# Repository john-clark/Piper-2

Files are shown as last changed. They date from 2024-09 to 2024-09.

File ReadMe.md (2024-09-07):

# ReadMe

Welcome to the Piper-2 Organization Project!

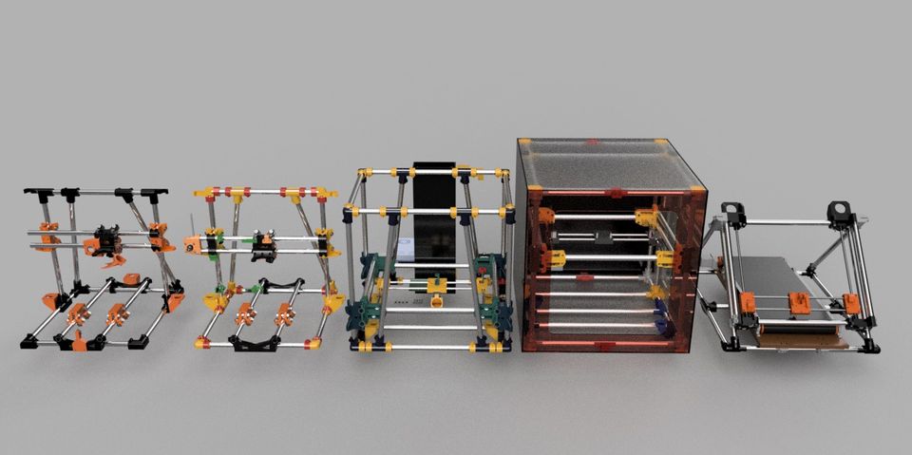
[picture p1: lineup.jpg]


## Description

Piper-3d is an exciting project that aims to revolutionize the world of low cost 3D engineering. It is a powerful tool that assists makers in high-quality 3D printer building using affordable and readily available parts. The Piper 3d printers are opensource and welcome contributions with a Creative Commons Share Alike license.

## Features

- US and European Electrical Conduit
- Different Build Platforms
- A variety of Design Features
- The latest advances in 3D printing technology

## Getting Started

To get started with Piper3D, follow these steps:

1. Clone the repository.
2. Open the Parts List table for your desired build.
3. Print and Checkoff parts as you aquire them.
4. Build your printer
5. Create new modifications and share them with others!

## Contribution

[Piper3printers](https://piper3dprinters.com/) started in 2016 by Alex Balako.

Designs are found on [Thingiverse/piper3d](https://www.thingiverse.com/piper3d/designs)

**I updated this repo to contain all the Piper3d related items I could find, so I could learn more and figure out what I need to print. This is not meant to be an official resource.*

## License

Piper-2 is licensed under the [Creative Commons - Attribution - Non-Commercial - Share Alikee](./LICENSE).

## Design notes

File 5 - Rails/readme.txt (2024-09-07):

This is work in progress on new Piper 5 3d printer

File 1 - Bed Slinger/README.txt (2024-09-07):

Piper 1 version 2 3D Printer by Piper3D on Thingiverse: 

EU - https://www.thingiverse.com/thing:2966295
US - https://www.thingiverse.com/thing:2999885

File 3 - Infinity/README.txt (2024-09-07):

Piper Infinity (Piper 4) - Infinite Z 3D Printer (Metric version or 19mm pipe)  by Piper3D on Thingiverse: https://www.thingiverse.com/thing:3817276
Piper Infinity (Piper 4) - Infinite Z 3D Printer (US version or 1/2 US EMT conduit) by Piper3D on Thingiverse: https://www.thingiverse.com/thing:3711685

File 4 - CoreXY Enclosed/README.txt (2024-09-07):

Piper 2 version 2 Enclosed CoreXY design based on EMT conduit pipes US version by Piper3D on Thingiverse: https://www.thingiverse.com/thing:3294998
Piper 2 version 2 Enclosed CoreXY design based on 20mm OD EMT conduit pipes UK by Piper3D on Thingiverse: https://www.thingiverse.com/thing:3303290

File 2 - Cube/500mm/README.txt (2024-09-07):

500mm+ upgrade for Piper 2 3d printer UK version  by Piper3D on Thingiverse: https://www.thingiverse.com/thing:3058435
500mm+ upgrade for Piper 2 3d printer US version by Piper3D on Thingiverse: https://www.thingiverse.com/thing:3051204

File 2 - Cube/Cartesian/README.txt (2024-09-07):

Piper 2 3D Printer (CoreXY design based on EMT conduit pipes) US version by Piper3D on Thingiverse: https://www.thingiverse.com/thing:3022836
Piper 2 3D Printer (CoreXY design based on EMT conduit pipes) 20mm OD Conduit version by Piper3D on Thingiverse: https://www.thingiverse.com/thing:3036472

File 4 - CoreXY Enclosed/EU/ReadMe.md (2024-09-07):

#### Summary

Piper 2.2 printing: <https://youtu.be/g6x3LBGErbc>

[Update: renamed "frame-corner-joint.stl" to "enclosure-frame-corner-joint.stl"]\
[Update: added gantry-motor-mount.nema23.stl and gantry-motor-mount.nema17.stl instead of gantry-motor-mount-.stl]\
[Update: added "gantry-Z_Rod_Nut_Holder.12mmRod.500+.stl" for 500+ build]\
[Update: combined regular and 500+ versions in one project, for parts which are different for 500+ version look for file names, which include "500+"]\
This is version 2 of Piper 2 3d printer uses 20mm OD conduit pipes. The version which uses 17.8mm OD may be found here: <https://www.thingiverse.com/thing:3294998>.\
Stepping into the area of enclosed printers with possibilities to print other materials like ABS and PolyCarbonate. Also utilizing new bearless Z bushings and new belt tension system.\
Assembly instructions are published at <https://piper3dprinters.com/?page_id=646>\
Since parts will work inside an enclosed environment with higher temperature I am using PETG as printing material.\
Printing quantities:\
6mm-belt-tensioner.stl - 2\
frame-3xcorner.stl - 8\
frame-3xcorner-bottom.stl - 8\
frame-4xcorner.stl - 4\
frame-4xcorner-bottom.stl -4\
frame-corner-joint.stl - 8\
frame-plate-holder.stl - 4\
frame-Z-motor-holder-left.stl - 2\
frame-Z-motor-holder-right.stl - 2\
frame-Z-motor-mount.stl - 4\
gantry-idlers-mount.stl - 2\
gantry-idlers-rod-holder.stl - 2\
gantry-motor-mount.stl - 2\
gantry-motor-mount-.stl - 2\
gantry-motor-rod-holder.stl - 2\
gantry-X-carriage.stl - 2\
gantry-Y-carriage.stl - 4\
gantry-ZRod-nut-holder.stl - 4\
gantry-Z-slider.stl - 4\
joint bracket.stl - 48\
bed mounting bracket 2.stl - 4\
bed mounting bracket.stl - 4\
gantry-X carriage-extruder mount fan blower.stl - 1\
gantry-X carriage-Fan holder.stl - 1\
gantry-X carriage-Heater holder.v1.2.stl - 1\
gantry-X carriage-Wire Holder.stl - 1\
gantry-Z Bracket.stl - 4\
universal pipe bracket.stl - 1 (For Z mechanical sensor mount.stl)\
Z mechanical sensor mount.stl - 1\
Y Sensor pin.stl - 1\
Join Piper builders on FB <https://www.facebook.com/groups/258663638022956/>

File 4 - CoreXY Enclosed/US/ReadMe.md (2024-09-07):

#### Summary

Piper 2.2 printing: <https://youtu.be/g6x3LBGErbc>\
[Update 02/20/2022] If you have difficulty downloading, files are also available at <https://github.com/piper3d?tab=repositories>\
[Update: Changing license and releasing source files]\
[Update: renamed "frame-corner-joint.stl" to "enclosure-frame-corner-joint.stl"]\
[Update: added gantry-X_carriage-Sensor_Pin.stl and X End Stop sensor mount mounts on Y carriage).stl]\
[Update: added gantry-motor-mount.nema23.stl and gantry-motor-mount.nema17.stl instead of gantry-motor-mount-.stl]\
[Update: added "gantry-Z_Rod_Nut_Holder.12mmRod.500+.stl" for 500+ build]\
[Update: combined regular and 500+ versions in one project, for parts which are different for 500+ version look for file names, which include "500+"]

Autodesk Fusion project for classic <https://a360.co/3qXlmPG>\
Autodesk Fusion project for enclosed <https://a360.co/3uo7hNz>\
or download igs files in "Piper 2.2 Classic v2.zip"

This is version 2 of Piper 2 3d printer. Stepping into the area of enclosed printers with possibilities to print other materials like ABS and PolyCarbonate. Also utilizing new bearless Z bushings and new belt tension system.

Assembly instructions are published at <https://piper3dprinters.com/?page_id=646>

Since parts will work inside an enclosed environment with higher temperature I am using PETG as printing material.

Printing quantities:\
6mm-belt-tensioner.stl - 2\
frame-3xcorner.stl - 8\
frame-3xcorner-bottom.stl - 8\
frame-4xcorner.stl - 4\
frame-4xcorner-bottom.stl -4\
frame-corner-joint.stl - 8\
frame-plate-holder.stl - 4\
frame-Z-motor-holder-left.stl - 2\
frame-Z-motor-holder-right.stl - 2\
frame-Z-motor-mount.stl - 4\
gantry-idlers-mount.stl - 2\
gantry-idlers-rod-holder.stl - 2\
gantry-motor-mount.stl - 2\
gantry-motor-mount-.stl - 2\
gantry-motor-rod-holder.stl - 2\
gantry-X-carriage.stl - 2\
gantry-Y-carriage.stl - 4\
gantry-ZRod-nut-holder.stl - 4\
gantry-Z-slider.stl - 4\
joint bracket.stl - 48\
bed mounting bracket 2.stl - 4\
bed mounting bracket.stl - 4\
gantry-X carriage-extruder mount fan blower.stl - 1\
gantry-X carriage-Fan holder.stl - 1\
gantry-X carriage-Heater holder.v1.2.stl - 1\
gantry-X carriage-Wire Holder.stl - 1\
gantry-Z Bracket.stl - 4\
universal pipe bracket.stl - 1 (For Z mechanical sensor mount.stl)\
Z mechanical sensor mount.stl - 1\
Y Sensor pin.stl - 1

Join Piper builders on FB <https://www.facebook.com/groups/258663638022956/>

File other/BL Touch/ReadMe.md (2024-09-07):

#### Summary

[Update: Added new version of the slider. got tired of them breaking and being inconsistent]\
This is a remix of "BlTouch Adjustable Mount" with adjusting screw of Imperial #6 size. Fits Piper 2 3D Printer.

For the adjustment mechanism you will need:\
1 - #6 2'' screw\
3 - #6 nuts.\
To mount BL touch:\
2 - #4 1/2'' screws\
2 - #4 nuts.

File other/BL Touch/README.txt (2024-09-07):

BL Touch Adjustable Mount for Piper 2 #6 screws by Piper3D on Thingiverse: https://www.thingiverse.com/thing:3170734

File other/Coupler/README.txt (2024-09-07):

Couplers for Z motors by Piper3D on Thingiverse: https://www.thingiverse.com/thing:3096142
Z couplings for Piper 3d printers and other 3d printers. 3 sizes for M8 thread, 5/16, and 3/8th.

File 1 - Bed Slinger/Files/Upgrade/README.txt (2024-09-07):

Piper 1 3D Printer version 3 upgrade by Piper3D on Thingiverse: https://www.thingiverse.com/thing:3539464

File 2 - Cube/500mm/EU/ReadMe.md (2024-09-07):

#### Summary

Large Piper 2: <https://youtu.be/ugT5Qs-Ho4Y>\
[Update: added X carriage for new version 2.2 belt tension "gantry-X_carriage-Extruder_Holder.12mmRods.v2.2.stl" and gantry-X_carriage-10mmbelt-tensioner.stl]

[Update: added Nema 23 mount for XY]

[Update: check v3 versions for gantry corner parts, changes are for motor side previous do not hold pipes; idler side was missing nut slots]

[Update: Found that some idlers for 10mm belt may be 14mm tall, please check new versions tagged "v1.1"]

[Update: Found problems with motor and idlers mounts. Fixed now as v2 files and 3mm bore and 5mm bore idleres]

By default, Piper 2 (<https://www.thingiverse.com/thing:3022836>) is designed to use 8mm guiding rods. Guiding rods will become unstable under belt tension if bed size will be stretched larger than 300mm. This upgrade allows the use of 12 mm rods and 10 mm GT2 belt. It should allow expansion of Piper 2 to a bed size beyond 300mm for example 500x500mm. Some dimensions have changed so bed size will be 123 mm less than Y rod and 113 mm less than X rod.

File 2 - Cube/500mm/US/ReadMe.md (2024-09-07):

#### Summary

[Update: added X carriage for new version 2.2 belt tension "gantry-X_carriage-Extruder_Holder.12mmRods.v2.2.stl" and gantry-X_carriage-10mmbelt-tensioner.stl]

[Update: added Nema 23 mount for XY]

Some of UK providers are still blocking the main website (they are slow to react) you may access mirror at <http://s728416714.onlinehome.us>.

[Update: check "v2" versions for gantry corner parts, changes are for motor side previous do not hold pipes; idler side was missing nut slots]

[Update: Found that some idlers for 10mm belt may be 14mm tall, please check new versions tagged "v1.1"]

This is 19.9 or 20mm pipe version upgrade (UK version).\
By default, Piper 2 (<https://www.thingiverse.com/thing:3036472>) is designed to use 8mm guiding rods. Guiding rods will become unstable under belt tension if bed size will be stretched larger than 300mm. This upgrade allows the use of 12 mm rods and 10 mm GT2 belt. It should allow expansion of Piper 2 to a bed size beyond 300mm for example 500x500mm. Some dimensions have changed so bed size will be 123 mm less than Y rod and 113 mm less than X rod.

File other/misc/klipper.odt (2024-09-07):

# This file serves as documentation for config parameters of corexy

# style printers. One may copy and edit this file to configure a new

# corexy printer. Only parameters unique to corexy printers are

# described here - see the "example.cfg" file for description of

# common config parameters.

# DO NOT COPY THIS FILE WITHOUT CAREFULLY READING AND UPDATING IT

# FIRST. Incorrectly configured parameters may cause damage.

# The main micro-controller is used as the timing source for all the

# micro-controllers on the printer. Typically, both the X and Y axes

# are connected to the main micro-controller.

[mcu]

serial: /dev/ttyACM0

#serial: /dev/serial/by-path/pci-0000:00:14.0-usb-0:2:1.0-port0

#serial: /dev/serial/by-path/pci-0000:00:14.0-usb-0:1:1.0-port0

#pin_map: arduino

#baud: 250000

# Support manually moving stepper motors for diagnostic purposes.

# Note, using this feature may place the printer in an invalid state -

# see docs/G-Codes.md for important details.

[force_move]

enable_force_move: true

# Set to true to enable FORCE_MOVE and SET_KINEMATIC_POSITION

# extended G-Code commands. The default is false.

# The "zboard" micro-controller will be used to control the Z axis.

[mcu z]

#serial: /dev/serial/by-path/pci-0000:00:14.0-usb-0:1:1.0-port0

#serial: /dev/serial/by-path/pci-0000:00:14.0-usb-0:2:1.0-port0

serial: /dev/ttyUSB0

pin_map: arduino

baud: 250000

#test INIT_TMC STEPPER=stepper_y DUMP_TMC STEPPER=stepper_y

[board_pins]

aliases:

# EXP1 header

EXP1_1=P1.30, EXP1_3=P1.18, EXP1_5=P1.20, EXP1_7=P1.22, EXP1_9=<GND>,

EXP1_2=P0.28, EXP1_4=P1.19, EXP1_6=P1.21, EXP1_8=P1.23, EXP1_10=<5V>,

# EXP2 header

EXP2_1=P0.17, EXP2_3=P3.26, EXP2_5=P3.25, EXP2_7=P1.31, EXP2_9=<GND>,

EXP2_2=P0.15, EXP2_4=P0.16, EXP2_6=P0.18, EXP2_8=<RST>, EXP2_10=<NC>

# Pins EXP2_1, EXP2_6, EXP2_2 are also MISO, MOSI, SCK of bus "ssp0"

# stepper controlling the X+Y movement.

[stepper_y]

step_pin: P0.19

dir_pin: !P0.20

enable_pin: !P2.8

#step_distance: 0.2

step_distance: 0.0125 #SHould be 0.0125 for 1/16 micro-steppting

##step_distance: 0.00625

endstop_pin: tmc2130_stepper_y:virtual_endstop

homing_retract_dist: 0

position_endstop: 0

position_min: 0

position_max: 500

homing_speed: 60

[tmc2130 stepper_y]

cs_pin: P1.15

spi_software_miso_pin: P0.5

spi_software_mosi_pin: P4.28

spi_software_sclk_pin: P0.4

diag1_pin: !P1.27

microsteps: 16

interpolate: True

run_current: .80 #Try 0.75 to 0.85 by 0.05 increments

hold_current: .5 #Set to 0.75

stealthchop_threshold: 0

driver_PWM_GRAD: 10

driver_SGT: 4

# The stepper_y section is used to describe the Y axis as well as the

# stepper controlling the X-Y movement.

[stepper_x]

step_pin: P2.2

dir_pin: P2.6

enable_pin: !P2.1

step_distance: 0.0125 #SHould be 0.0125 for 1/16 micro-steppting

#step_distance: 0.00625

endstop_pin: tmc2130_stepper_x:virtual_endstop

homing_retract_dist: 0

position_endstop: 0

position_max: 500

position_min: 0

homing_speed: 60

[tmc2130 stepper_x]

cs_pin: P1.17

spi_software_miso_pin: P0.5

spi_software_mosi_pin: P4.28

spi_software_sclk_pin: P0.4

diag1_pin: !P1.29

microsteps: 16

interpolate: True

run_current: .80 #Try 0.75 to 0.85 by 0.05 increments

hold_current: .5 #Set to 0.75

#run_current: 1.2 #Try 0.75 to 0.85 by 0.05 increments

#hold_current: .5 #Set to 0.75

#sense_resistor: 0.110

stealthchop_threshold: 0

driver_PWM_GRAD: 10

driver_SGT: 11

[stepper_z]

# Z stepper pins on MCU Z

step_pin: z:ar60

dir_pin: z:ar61

enable_pin: !z:ar56

step_distance: 0.000625

# probe:z_virtual_endstop is a virtual pin definition only available if

# a probe section is defined

endstop_pin: probe:z_virtual_endstop

# mechanical switch on mcu Z X min endstop pin

##endstop_pin: ^!z:ar19

#position_endstop: -0.376

position_min: -5

position_max: 500

homing_speed: 5

[stepper_z1]

# X stepper pins on MCU Z

step_pin: z:ar54

dir_pin: z:ar55

enable_pin: !z:ar38

step_distance: 0.000625

[stepper_z2]

# E0 stepper pins on MCU Z

step_pin: z:ar26

dir_pin: z:ar28

enable_pin: !z:ar24

step_distance: 0.000625

[stepper_z3]

# E0 stepper pins on MCU Z

step_pin: z:ar46

dir_pin: z:ar48

enable_pin: !z:ar62

step_distance: 0.000625

#[servo toolS]

#pin: z:ar42

#maximum_servo_angle: 300

### The maximum angle (in degrees) that this servo can be set to. The

### default is 180 degrees.

##minimum_pulse_width: 0.0005

### The minimum pulse width time (in seconds). This should correspond

### with an angle of 0 degrees. The default is 0.001 seconds.

#maximum_pulse_width: 0.003

#initial_angle: 120

[probe]

pin: ^!z:ar18

z_offset: 1.82

y_offset: 5

x_offset: 0

speed: 5.0

#[homing_override]

#set_position_z: 0

#axes: z

#gcode:

# G90 ; Uncomment these 2 lines to blindly lift the Z 2mm at start

# G1 Z10 F600

# G28 X0 Y0

# G1 X250 Y250 F3600

# G28 Z0

[homing_override]

set_position_z: 0

axes: z

gcode:

G90 ; Uncomment these 2 lines to blindly lift the Z 2mm at start

G1 Z8 F600

G28 X0 Y0

G1 X250 Y250 F3600

G28 Z0

G1 Z10 F600

#[temperature_sensor Host_temp]

#sensor_type: temperature_host

#sensor_path: /sys/bus/platform/drivers/coretemp/coretemp.0/hwmon/hwmon1/temp2_input

#gcode_id:S

[adc_temperature my_sensor]

#temperature1: 28

#voltage1: 0.8

temperature1: 26.5

voltage1: 0.822

temperature2: 50.3

voltage2: 0.914

temperature3: 75.5

voltage3: 1.012

temperature4:100.6

voltage4:1.106

temperature5:150.4

voltage5:1.289

temperature6:200.1

voltage6:1.464

temperature7:225.1

voltage7:1.547

temperature8:250.8

voltage8:1.623

#temperature1: 221

#resistance1:

#temperature2:

#resistance2:

[thermistor winsinn_ht-ntc100k]

temperature1: 25

resistance1: 100000

temperature2: 80

resistance2: 8300

temperature3: 220

resistance3: 127

[extruder]

step_pin: P2.13

dir_pin: !P0.11

enable_pin: !P2.12

#step_distance: 0.010476

step_distance: 0.0024145313708312

nozzle_diameter: 0.400

filament_diameter: 1.750

max_extrude_cross_section: 20.0

max_extrude_only_distance: 950.0

max_extrude_only_accel: 10000

#pressure_advance: 0.0

#pressure_advance_lookahead_time: 0.010

#pressure_advance: 0.45

#pressure_advance_lookahead_time: 0.02

heater_pin: P2.7

######sensor_type: winsinn_ht-ntc100k

######sensor_pin: P0.24

######pullup_resistor: 4700

######sensor_type: ATC Semitec 104GT-2

sensor_type: NTC 100K beta 3950

sensor_pin: P0.24

#sensor_type: PT100 INA826

#adc_voltage: 3.2

#sensor_pin: P0.2

#voltage_offset: 0.48

#PT100

#sensor_type: my_sensor

#adc_voltage: 3.275

#sensor_pin: P0.2

#sensor_type: NTC 100K beta 3950

#sensor_type: EPCOS 100K B57560G104F

#sensor_type: NTC 100K MGB18-104F39050L32

#sensor_type: Honeywell 100K 135-104LAG-J01

#control: watermark

min_temp: 0

max_temp: 500

#[extruder1]

#step_pin: z:ar36

#dir_pin: !z:ar34

#enable_pin: !z:ar30

#step_distance: 0.0024145313708312

#nozzle_diameter: 0.400

#filament_diameter: 1.750

#max_extrude_cross_section: 20.0

#max_extrude_only_distance: 950.0

#max_extrude_only_accel: 10000

#pressure_advance: 0.0

#pressure_advance_lookahead_time: 0.010

#pressure_advance: 0.45

#pressure_advance_lookahead_time: 0.02

#heater_pin: z:ar10

#sensor_pin: z:analog13

##sensor_type: ATC Semitec 104GT-2

#sensor_type: NTC 100K beta 3950

#sensor_type: EPCOS 100K B57560G104F

#sensor_type: NTC 100K MGB18-104F39050L32

#sensor_type: Honeywell 100K 135-104LAG-J01

#control: watermark

#min_temp: 0

#max_temp: 300

#pid_Kp: 22.2

#pid_Ki: 1.08

#pid_Kd: 114

[heater_fan my_nozzle_fan]

pin: z:ar9

heater: extruder

heater_temp: 50.0

fan_speed: 1.0

[heater_bed]

heater_pin: P2.5

sensor_type: NTC 100K beta 3950

sensor_pin: P0.23

#control: watermark

min_temp: 0

max_temp: 150

[verify_heater heater_bed]

# adjust for personal bed setup, this prevents stock heated bed from issuing

# false positive heating errors due to slow temperature increase

check_gain_time: 900

[verify_heater extruder]

check_gain_time: 120

heating_gain: 1

max_error: 260

#[verify_heater extruder1]

#check_gain_time: 60

[temperature_sensor ambiant]

sensor_type: ATC Semitec 104GT-2

sensor_pin: P0.25

gcode_id:A

[fan]

pin: P2.3

# Load Multible Fans

#[include klipper/config/multiple_fans.cfg]

[printer]

kinematics: corexy

# This option must be "corexy" for corexy printers.

max_velocity: 250

max_accel: 1500

#max_z_velocity: 20

#max_z_accel: 25

max_z_velocity: 10

max_z_accel: 55

# "RepRapDiscount 128x64 Full Graphic Smart Controller" type displays

[display]

lcd_type: st7920

cs_pin: P1.19

sclk_pin: P1.20

sid_pin: P1.18

encoder_pins: ^P3.26, ^P3.25

click_pin: ^!P0.28

[output_pin beeper]

pin: P1.30

#kill_pin: ^!ar41

# Pause/Resume functionality with support of position capture and restore

[pause_resume]

recover_velocity: 50

#recover_velocity: 200

# When capture/restore is enabled, the speed at which to return to

# the captured position (in mm/s). Default is 50.0 mm/s.

# paste "unknownCommandsNeedAck: true" in ~/.octoprint/config.yaml

# serial: #

# additionalPorts: #

# - /tmp/printer #

# baudrate: 250000 #

# disconnectOnErrors: false #

# logPositionOnCancel: true #

# port: /tmp/printer #

# unknownCommandsNeedAck: true #

# Filament Switch Sensor. Support for filament insert and runout detection

# using a switch sensor, such as an endstop switch.

[filament_switch_sensor filament_sensor]

pause_on_runout: True

# When set to True, a PAUSE will execute immediately after a runout

# is detected. Note that if pause_on_runout is False and the

# runout_gcode is omitted then runout detection is disabled. Default

# is True.

runout_gcode: outoffilament

# The gcode to run after a filament runout is detected. If

# pause_on_runout is set to True this gcode will run after the PAUSE

# is complete. The default is not to run any gcode commands.

#insert_gcode:

# The gcode to run after a filament insert is detected. The default

# is not to run any gcode commands, which disables insert detection.

event_delay: 3.0

# The minimum amount of time in seconds to delay between events.

# Events triggered during this time period will be silently

# ignored. The default is 3 seconds.

switch_pin: ^z:ar15 #RAMPS Servo Pin 4

# The pin on which the switch is connected. This parameter must be

# provided.

# Idle timeout. An idle timeout is automatically enabled - add an

# explicit idle_timeout config section to change the default settings.

[idle_timeout]

#gcode:

# A list of G-Code commands (one per line; subsequent lines

# indented) to execute on an idle timeout. The default is to run

# "TURN_OFF_HEATERS" and "M84".

#timeout: 600

timeout: 1200

# Idle time (in seconds) to wait before running the above G-Code

# commands. The default is 600 seconds

#_____________________MACROS______________________________________#

#_____________________MACROS______________________________________#

[gcode_macro outoffilament]

gcode:

PARK_MACRO

;UNLOAD

M117 OUT OF FILAMENT..

[gcode_macro PARK_MACRO]

default_parameter_X: -15

default_parameter_Y: 0

default_parameter_Z: 30

gcode:

M117 PARKING..

G91

G1 E-3.14 F1500

G1 Z{Z}

G90

G1 X{X} Y{Y} F3000

[gcode_macro UNLOAD]

gcode:

G91

G1 E5.0 F1200

G1 E3.0 F1600

G1 E-25 F7000

G1 E-800 F3000

G90

[gcode_macro RESUME_MACRO]

gcode:

M117 RESUMING...

RESUME

#[gcode_macro M84]

#gcode:

# M18

# SET_KINEMATIC_POSITION

# Enable the "M118" and "RESPOND" extended commands.

[respond]

default_type: echo

# Sets the default prefix of the "M118" and "RESPOND" output to one of

# the following:

# echo: "echo: " (This is the default)

# command: "// "

# error: "!! "

# default_prefix: echo:

# Directly sets the default prefix. If present, this value will override

# the "default_type".

[gcode_macro G29]

gcode:

G28

quad_gantry_level

BED_MESH_CALIBRATE

BED_MESH_PROFILE SAVE=p1

G1 X0 Y0 Z5 F3600

[quad_gantry_level]

gantry_corners:

-90,-22.5

590,495

points:

20,40

20,440

450,440

450,40

speed: 50

horizontal_move_z: 10

max_adjust: 12

#samples: 3

#sample_retract_dist: 2.0

#[quad_gantry_level]

#gantry_corners:

# 0,0

# 300,300

## -88,-20

# 490,386

# A newline separated list of X,Y coordinates describing the

# two opposing corners of the gantry. The first entry corresponds to

# Z, the second to Z2.

# This parameter must be provided.

#points:

# 10,63

# 10,326

# 290,326

# 290,63

# A newline separated list of four X,Y points that should be probed

# during a QUAD_GANTRY_LEVEL command.

# Order of the locations is important, and should correspond to Z,Z1

# Z2, and Z3 location in order.

# This parameter must be provided.

# For maximum accuracy, ensure your probe offsets are configured.

#speed: 50

###speed: 150

# The speed (in mm/s) of non-probing moves during the calibration.

# The default is 50.

#horizontal_move_z: 10

# The height (in mm) that the head should be commanded to move to

# just prior to starting a probe operation. The default is 5

#samples: 3

# Number of probe samples per point. The defaut is 1

#sample_retract_dist: 6.0

# Distance in mm to retract the probe between samples. Default is 2.

# Mesh Bed Leveling. One may define a [bed_mesh] config section

# to enable move transformations that offset the z axis based

# on a mesh generated from probed points. Note that bed_mesh

# and bed_tilt are incompatible, both cannot be defined. When

# using a probe to home the z-axis, it is recommended to define

# a [homing_override] section in printer.cfg to home toward the

# center of the print area.

# Visual Examples:

# bed_shape = rectangular, probe_count = 3,3:

# x---x---x (max_point)

# x---x---x

# (min_point) x---x---x

# bed_shape = round, probe_count = 5, radius = r:

# x (0,r) end

# /

# x---x---x

# \

# (-r,0) x---x---x---x---x (r,0)

# \

# x---x---x

# /

# x (0,-r) start

[bed_mesh]

speed: 200

# The speed (in mm/s) of non-probing moves during the

# calibration. The default is 50.

horizontal_move_z: 10

# The height (in mm) that the head should be commanded to move to

# just prior to starting a probe operation. The default is 5.

#samples: 2

# The number of times to probe each point. The probed z-values

# will be averaged. The default is to probe 1 time.

#sample_retract_dist: 10.0

# The distance (in mm) to retract between each sample if

# sampling more than once. Default is 2mm.

mesh_min: 45,25

# Defines the minimum x,y position to probe when the bed_shape

# is 'rectangular'. Note that this refers to the nozzle position,

# take care that you do not define a point that will move the

# probe off of the bed. This parameter must be provided.

mesh_max:445,440

# Defines the maximum x,y position to probe when the bed_shape

# is 'rectangular'. Follow the same precautions as listed in min_point.

# Also note that this does not necessarily define the last point

# probed, only the maximum coordinate. This parameter must be provided.

probe_count: 4,4

## OR ##

##probe_count: 5

# For 'rectangular' beds, this is a comma separate pair of integer

# values (X,Y) defining the number of points to probe along each axis.

# A single value is also valid, in which case that value will be applied

# to both axes. 'Round' beds only accept a single integer value that is

# applied to both axes. The probe count must be odd for round beds.

# Default is 3,3 for 'rectangular' beds, and 5 for 'round' beds.

fade_start: 1

# The gcode z position in which to start phasing out z-adjustment

# when fade is enabled. Default is 1.0.

#fade_end: 10.0

fade_end: 0.0

# The gcode z position in which phasing out completes. When set

# to a value below fade_start, fade is disabled. It should be

# noted that fade may add unwanted scaling along the z-axis of a

# print. If a user wishes to enable fade, a value of 10.0 is

# recommended. Default is 0.0, which disables fade.

# disabling fade as per https://github.com/KevinOConnor/klipper/issues/1234

fade_target: 0

# The z position in which fade should converge. When this value is set

# to a non-zero value it must be within the range of z-values in the mesh.

# Users that wish to converge to the z homing position should set this to 0.

# Default is the average z value of the mesh.

split_delta_z: .025

# The amount of Z difference (in mm) along a move that will

# trigger a split. Default is .025.

move_check_distance: 5.0

# The distance (in mm) along a move to check for split_delta_z.

# This is also the minimum length that a move can be split. Default

# is 5.0.

#mesh_pps: 2,2

# A comma separated pair of integers (X,Y) defining the number of

# points per segment to interpolate in the mesh along each axis. A

# "segment" can be defined as the space between each probed

# point. The user may enter a single value which will be applied

# to both axes. Default is 2,2.

algorithm: bicubic

#algorithm: lagrange

# The interpolation algorithm to use. May be either "lagrange"

# or "bicubic". This option will not affect 3x3 grids, which

# are forced to use lagrange sampling. Default is lagrange.

bicubic_tension: .2

# When using the bicubic algorithm the tension parameter above

# may be applied to change the amount of slope interpolated.

# Larger numbers will increase the amount of slope, which

# results in more curvature in the mesh. Default is .2.

#*# <---------------------- SAVE_CONFIG ---------------------->

#*# DO NOT EDIT THIS BLOCK OR BELOW. The contents are auto-generated.

#*#

#*# [extruder]

#*# control = pid

#*# pid_kp = 21.512

#*# pid_ki = 1.304

#*# pid_kd = 88.737

#*#

#*# [heater_bed]

#*# control = pid

#*# pid_kp = 67.840

#*# pid_ki = 2.432

#*# pid_kd = 473.183

#*#

#*# [bed_mesh default]

#*# version = 1

#*# points =

#*# 0.292233, 0.530983, 0.431608, 0.330983

#*# 0.245358, 0.544733, 0.115358, -0.540267

#*# -0.080892, 0.474733, -0.063392, -1.140892

#*# -0.745267, 0.477233, 0.227233, -1.215892

#*# tension = 0.2

#*# min_x = 45.0

#*# algo = bicubic

#*# y_count = 4

#*# mesh_y_pps = 2

#*# min_y = 25.0

#*# x_count = 4

#*# max_y = 439.99

#*# mesh_x_pps = 2

#*# max_x = 444.99

#*#

#*# [bed_mesh p1]

#*# version = 1

#*# points =

#*# 0.292233, 0.530983, 0.431608, 0.330983

#*# 0.245358, 0.544733, 0.115358, -0.540267

#*# -0.080892, 0.474733, -0.063392, -1.140892

#*# -0.745267, 0.477233, 0.227233, -1.215892

#*# tension = 0.2

#*# min_x = 45.0

#*# algo = bicubic

#*# y_count = 4

#*# mesh_y_pps = 2

#*# min_y = 25.0

#*# x_count = 4

#*# max_y = 439.99

#*# mesh_x_pps = 2

#*# max_x = 444.99

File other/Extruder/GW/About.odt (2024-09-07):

#### Summary

I like GW extruder and saw some ways to improve it. Indeed all my current Piper printers (https://www.thingiverse.com/thing:2794632) are running on this version or AJGW extruders.
Problems I tried to fix are: E3D hotend is mounted on 2 screws and moves after some use; closing filament clamp (compressor... name it) may jam filament. Have added a new fast release, which works better for me opens and closes easier. Included mounts for Bowden tube and for E3D hotend.
Autocad Fusion 360 project may be found at: https://a360.co/2Iu8v5x or downloaded as part of all files. Autocad assembly contains components from McMaster webpage, E3D from https://www.thingiverse.com/thing:341689 , and I do not remember the source of NEMA 17 component.

Quick release in action: https://youtu.be/Ad7Fl6Ia978

As noted by Alain idler mount, which I call "filament compressor" may need to be printed on a side.

You may also check my website https://piper3dprinter.com for other things I do.

#### Post-Printing

You will also need:
3 - 608 ball bearings
1 - 18mm pin (may be a rod cut from a bolt) 5/16 or M8 to mount ball bearing in the "compressor" (idler)
2 - M4 50mm not fully threaded bolts for quick release
2 -1/4 in x0.5 in x0.035 in (6.4 mm x12 mm x0.9mm) (maybe other which will slide on M4 and held by M4 head) compression springs
1 - Nema 17 motor
1 - Hobbed bolt 5/16 or M8 (check my things for a tool to make one)
2 - nuts 5/16 or M8 to lock hobbed bolt
3 - M3 8mm bolts to hold the motor
1 - #6 1.5 in or M4 30 mm bolt and nut to hold idler ("compressor")
2 - #4 3/4 in or M3 18-20mm screws and nuts for E3D or Bowden mount.

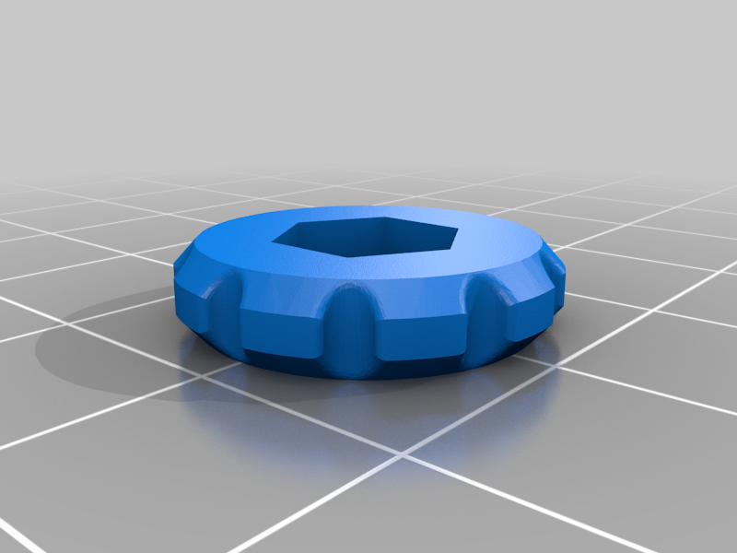
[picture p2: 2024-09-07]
other/BL Touch/images/ed52c49a278d1c5375fa5901e04589cf.png

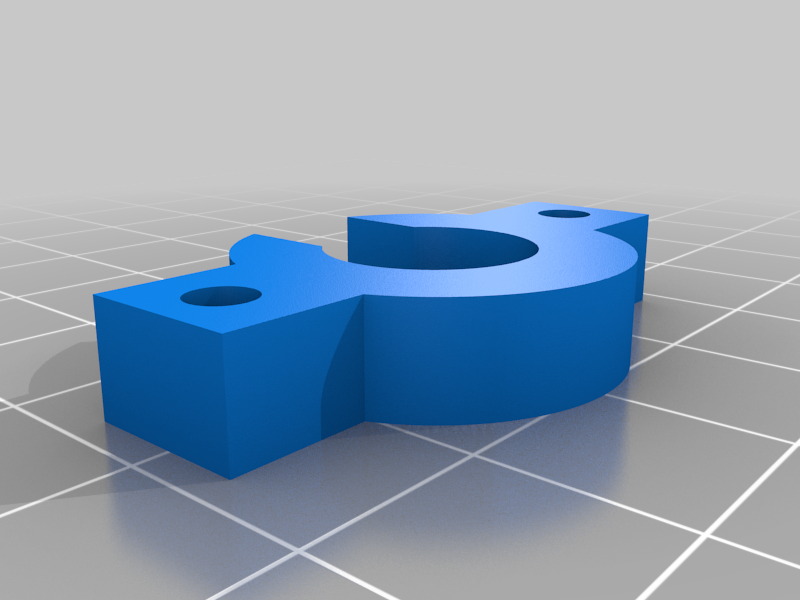
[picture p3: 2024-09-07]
other/Extruder/GW/images/3adc9352149461a922bf1bfca814c3d4.png

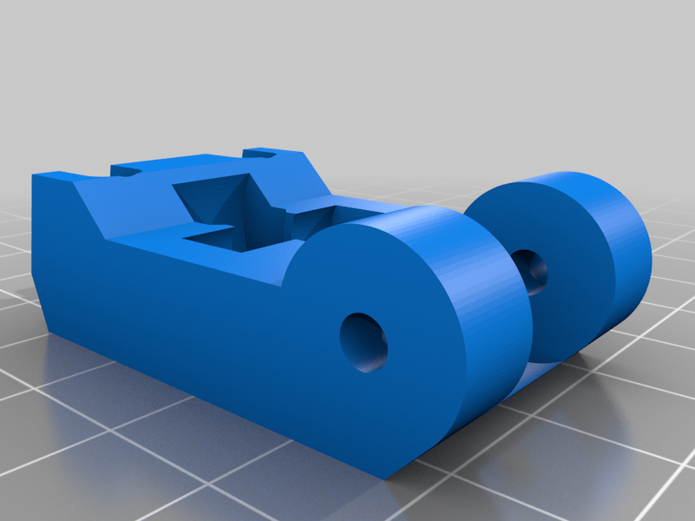
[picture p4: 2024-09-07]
other/Extruder/GW/images/1d85b2dbc3a063c84c43cf215b9fdd03.png

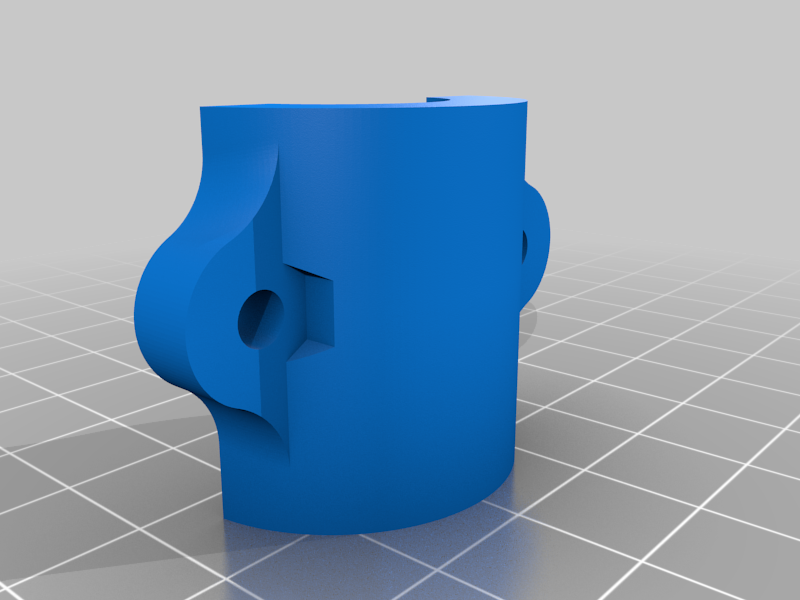
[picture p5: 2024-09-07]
other/Extruder/Titan/images/5b3e2f775d2780d6d07a16652f02b827.png

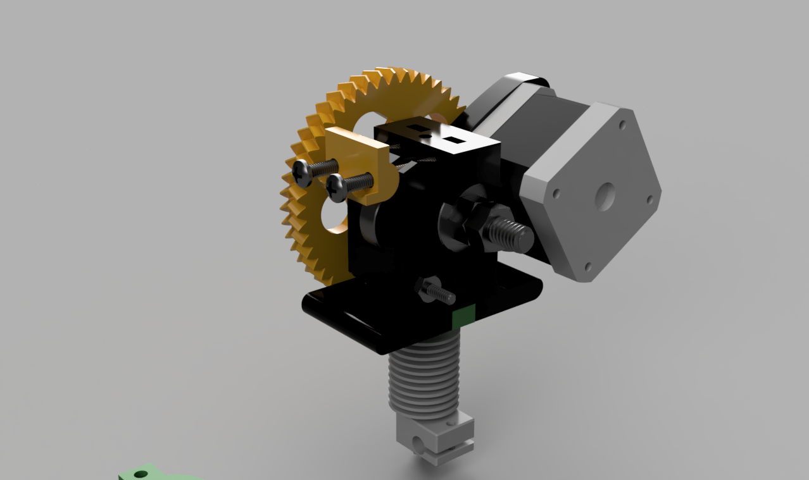
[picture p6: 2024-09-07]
other/Extruder/GW/images/new_extruder_2018-May-19_01-11-48AM-000_CustomizedView87308378.png

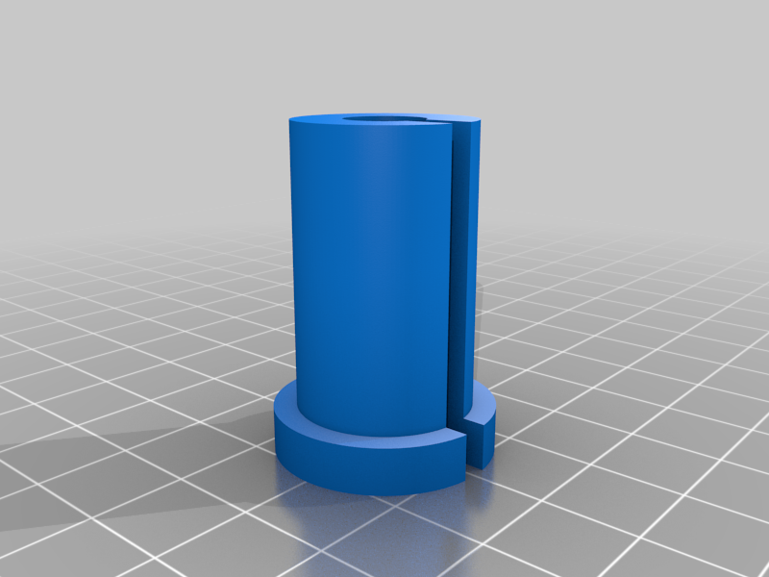
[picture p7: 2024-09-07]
1 - Bed Slinger/Files/Upgrade/images/1d4518fa89982501eb0c6e300d231709.png

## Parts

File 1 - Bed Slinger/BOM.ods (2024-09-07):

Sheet: BOTH
For both SAE and Metric:
Part | Quantities | Part example link
For the printer frame:
608 ball bearings | 35 | 608
Idler Pulley 20 teeth 5mm ID | 2 | Idler Pulley
GT2 belt |  | belt
End stop sensors | 3 | sensor
GT2 Timing Belt Pulley 5mm Bore 6mm Width | 2 | Motor Pulley
Nema 17 motors | 4
M3 8-10mm bolts for NEMA motors | 16
RAMPS 1.4 board | 1 | ramps 1.4
Arduino board | 1 | arduino
Or instead of Ramps and Arduino single 32 bit board |  | SKR 1.3
driver board A4988 or DRV8825 | 4 | A4988 DRV8825
12V PSU | 1 | PSU
40 mm fan | 1 | fan
For Extruder:
Nema 17 motors | 1
608 ball bearings | 2
5/16 2 1/2 inch bolt for lead screw | 1
5/16 nuts | 2
Extruder head | 1 | head

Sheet: EU
METRIC –
Metal Pipes with OD 17.8-18.5mm:
Other Parts
METRIC:
Fastener | Quantities | Part example link
M8 25mm Bolts | 23
M8 40mm bolts | 10
M8 Nuts | 33
M4 20mm bolts | 40
M4 12mm bolts | 22
M5 25mm screws for pulleys | 2
M5 nuts | 2
M3 8-10mm bolts for NEMA motors | 16
Part | Qty | 200x300x200 build | 300x300x300 (1 CF) build | 400x400x400 build | 500x500x500 build
Base front along X axis | 1 | 385mm | 485mm | 631mm | 777mm
Base back along X axis | 1 | 367mm | 467mm | 613mm | 759mm
Base along Y axis | 2 | 400mm | 426mm | 526mm | 627mm
Y rails | 2 | 477mm | 503mm | 603mm | 703mm
X rails | 2 | 477mm | 577mm | 723mm | 869mm
Z rails | 2 | 427mm | 527mm | 627mm | 727mm
Top along X axis | 1 | 385mm | 485mm | 631mm | 777mm
Z support | 2 | 446mm | 552mm | 658mm | 764mm
Lead screw length version 1 | 2 | 420mm+ | 510mm+ | 610mm+ | 710mm+
Lead screw length version 2 | 2 | 410mm+ | 500mm+ | 600mm+ | 700mm+

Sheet: US
SAE –
Conduit pipes 1/2 inch diameter 0.7 inch/17.8mm OD:
Other parts:
SAE:
Fastener | Quantities | Part example link
5/16 1 inch bolts | 23
5/16 1.5 inch bolts | 10
5/16 nuts | 33
#6 3/4 screws | 40
#6 1/2 inch screws | 22
#6 nuts | 62
#10 1 inch screws for pulleys | 2
#10 nuts | 2
What You Need (SAE - US) |  | 200x300x200 | 300x300x300 | 400x400x400 | 500x500x500
Part | Qty | Inches | Inches | Inches | Inches
Base Front Along X Axis | 1 | 14 3/32 | 19 3/32 | 23 1/32 | 26 31/32
Base Back Along X Axis | 1 | 14 29/64 | 18 25/64 | 22 21/64 | 26 17/64
Base Along Y Axis | 2 | 15 3/4 | 16 49/64 | 20 43/64 | 24 11/16
Y Rails | 2 | 18 25/32 | 19 51/64 | 23 47/64 | 27 43/64
X Rails | 2 | 18 25/32 | 22 23/32 | 26 21/32 | 30/19/32
Z Rails | 2 | 16 3/16 | 20 3/4 | 24 11/16 | 28 5/8
Top Along X Axis | 1 | 15 5/32 | 19 3/32 | 23 1/32 | 26 31/32
Z Support | 2 | 17 9/16 | 21 1/2 | 25 55/64 | 30 5/64
Lead Screw Length Version 1 | 2 | 16 17/32 | 20 5/64 | '24/1/64 | 27 61/64
Lead Screw Length Version 2 | 2 | 16 9/64 | 19 11/16 | 23 5/8 | 27 9/16

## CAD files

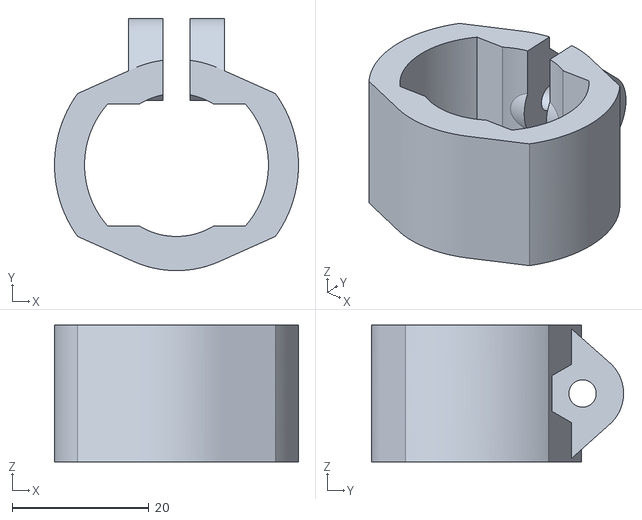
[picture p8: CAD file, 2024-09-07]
1 - Bed Slinger/Files/EU - Metric 19mm pipe/joint_bracket.19.9mm.stl
35.7 x 36.9 x 20.0

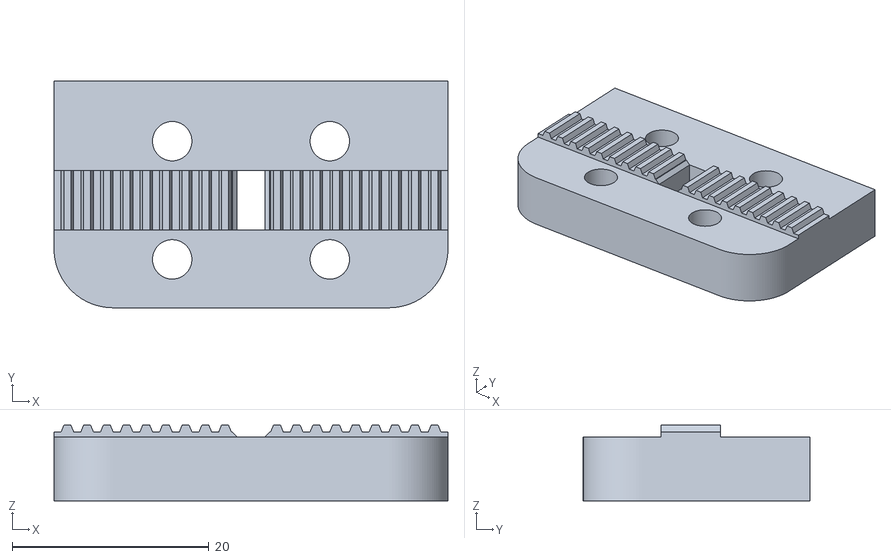
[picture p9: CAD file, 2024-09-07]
1 - Bed Slinger/Files/Other/Gantry/BeltHolder.stl
40.0 x 23.0 x 7.67

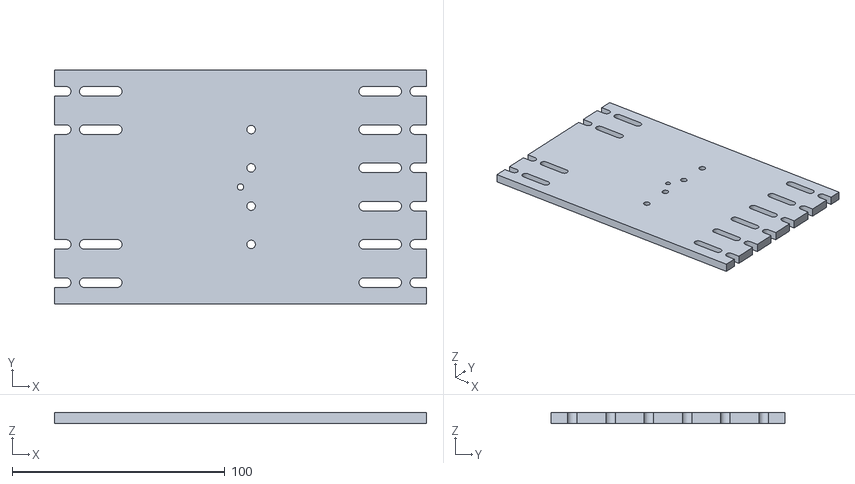
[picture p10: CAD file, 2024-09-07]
1 - Bed Slinger/Files/Other/template_for_bed_piper1.stl
175.0 x 110.0 x 5.00

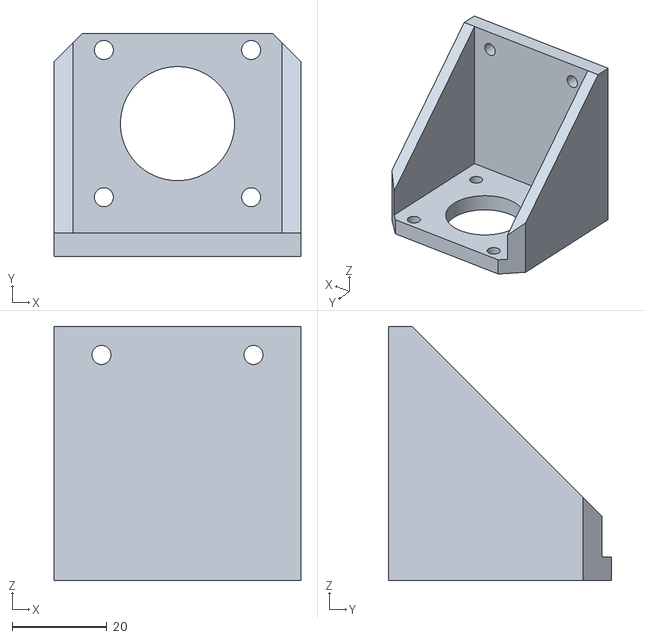
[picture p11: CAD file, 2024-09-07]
1 - Bed Slinger/Files/Shared/Y_Motor_Mount.stl
52.0 x 47.0 x 53.5

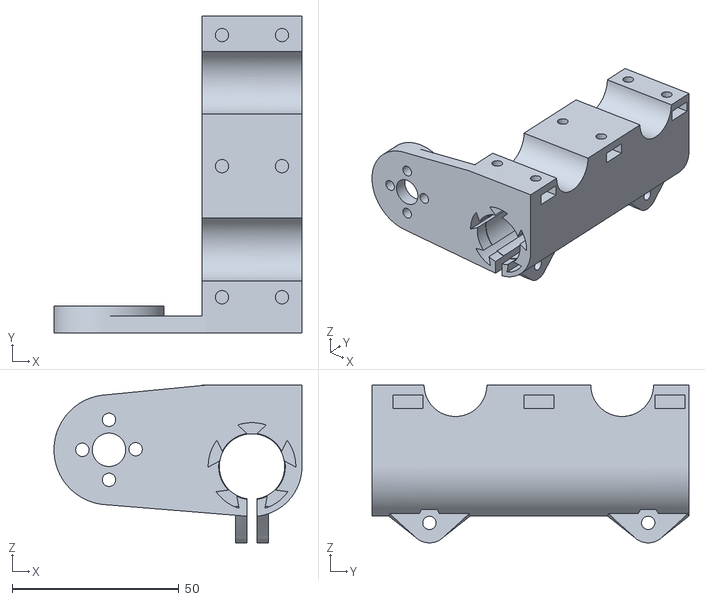
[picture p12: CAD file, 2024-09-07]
1 - Bed Slinger/Files/Upgrade/files/Z_Slider_Experimental.stl
74.4 x 95.0 x 47.3

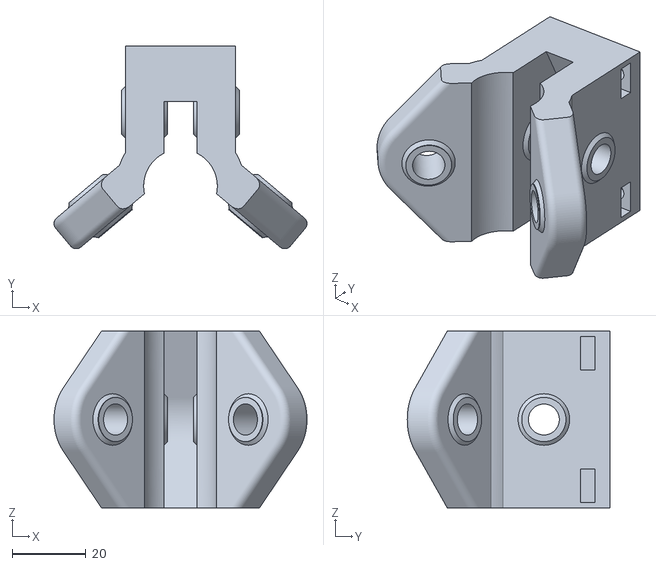
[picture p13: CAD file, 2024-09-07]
1 - Bed Slinger/Files/US - 12 US EMT conduit/XRoller_alternative_US.stl
68.7 x 55.0 x 48.0

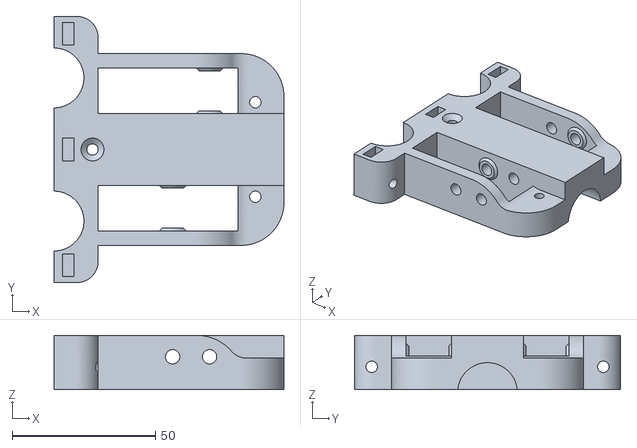
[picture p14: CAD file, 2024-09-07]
2 - Cube/500mm/EU/gantry-idler_outside.12mmRod.5mmbore.v2.stl
80.4 x 93.0 x 19.0

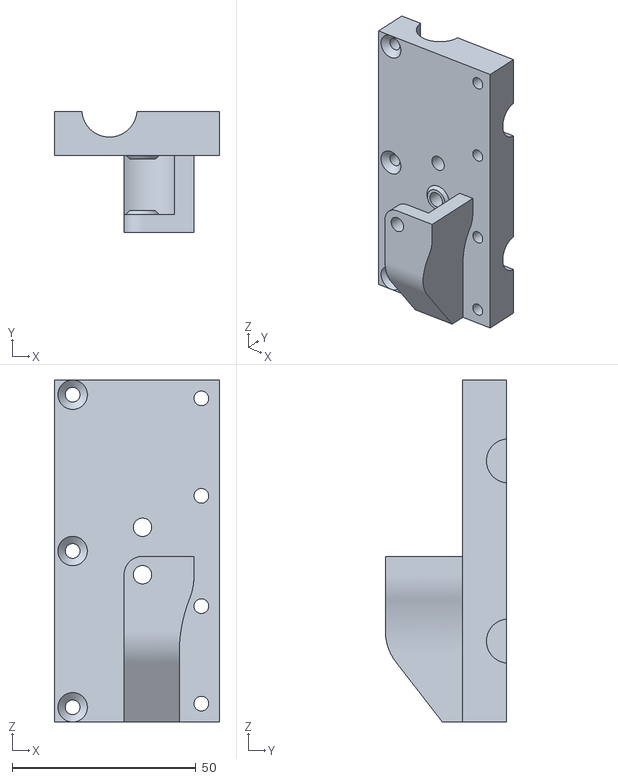
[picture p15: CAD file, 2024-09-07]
2 - Cube/500mm/Shared/gantry-Y_carriage.12mmRod.5mmbore.v1.1.stl
45.0 x 33.0 x 93.0

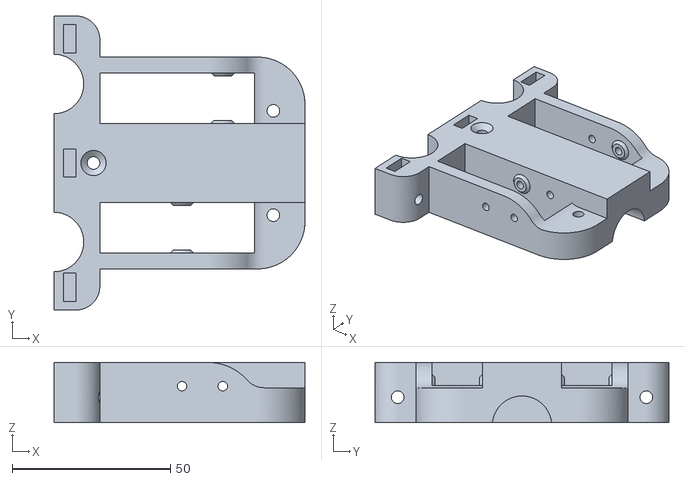
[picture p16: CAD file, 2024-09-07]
2 - Cube/500mm/US/gantry-idler_outside.12mmRod.3mmbore.v3.stl
79.4 x 93.0 x 19.0

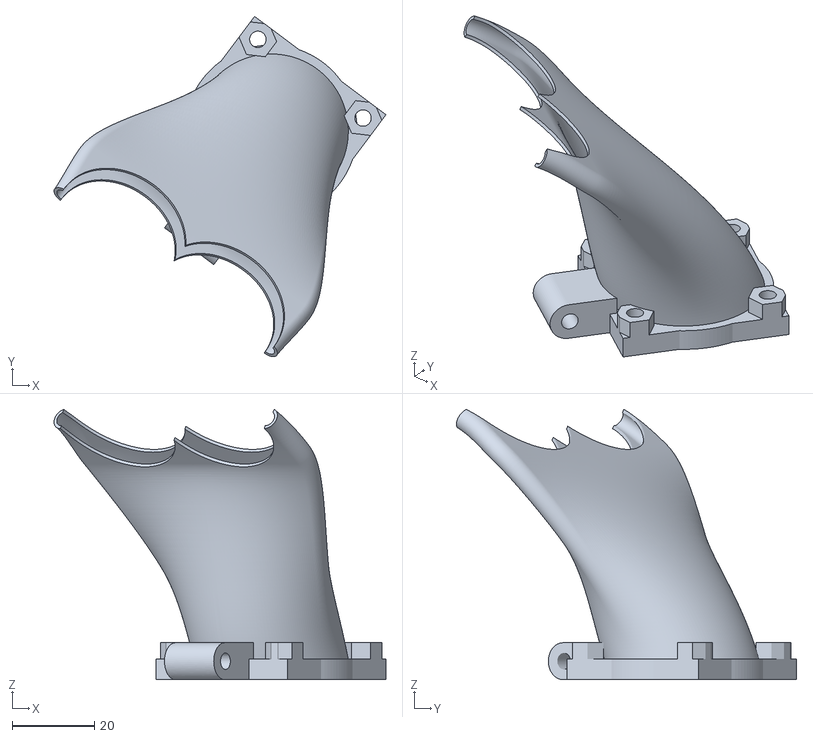
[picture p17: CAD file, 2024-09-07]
2 - Cube/Cartesian/EU/gantry-X_carriage-dual_extruder_mount_fan_blower.stl
80.9 x 82.9 x 65.9

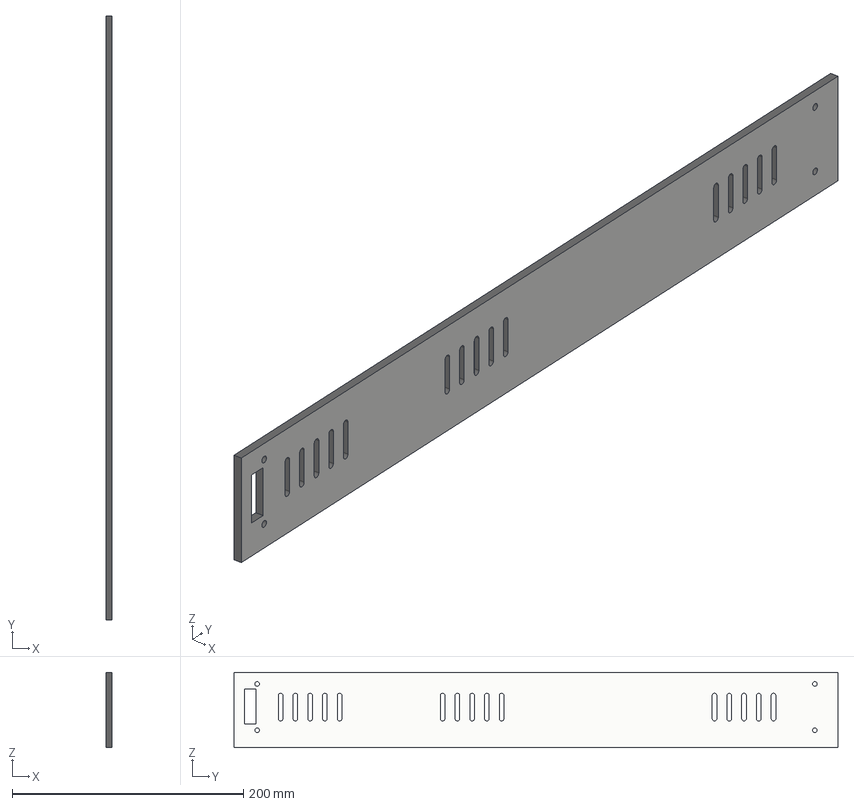
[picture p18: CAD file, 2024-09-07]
2 - Cube/Cartesian/shared/enclosure-_Left.step
5.00 x 522.0 x 65.0 mm

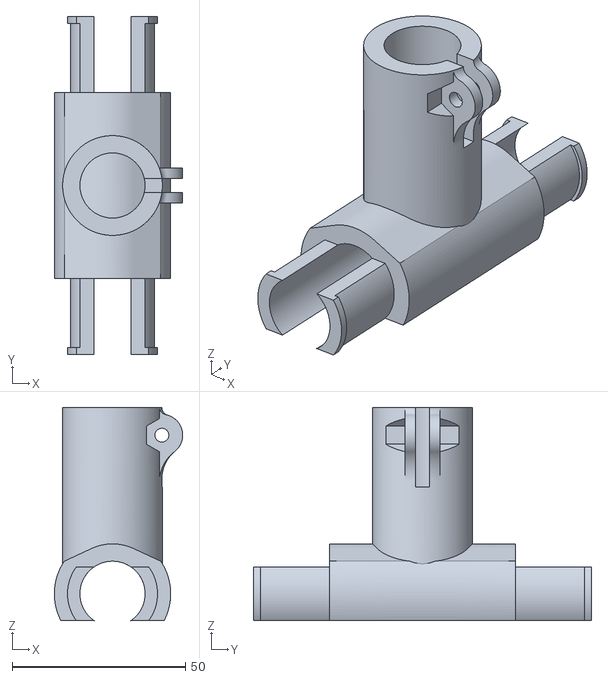
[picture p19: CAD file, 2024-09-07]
2 - Cube/Cartesian/US/frame-Z_2x_corner.stl
37.1 x 97.6 x 61.5

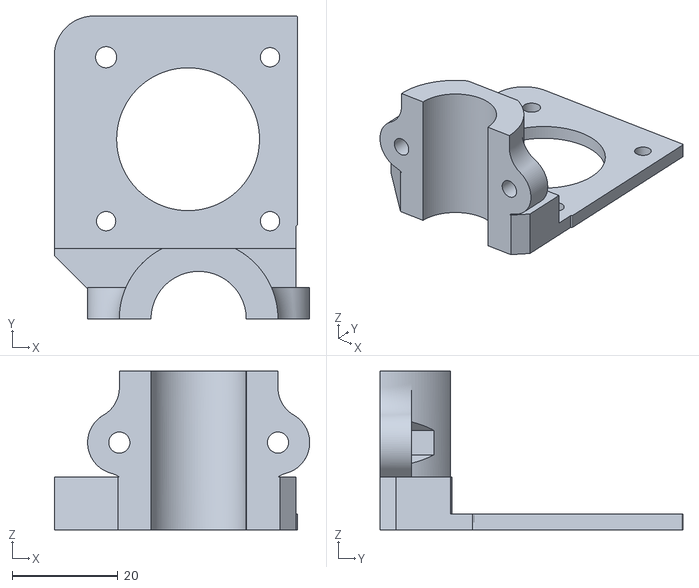
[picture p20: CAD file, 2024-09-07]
2 - Cube/CoreXY/STL/US/Titan extruder Mount top.stl
48.3 x 57.3 x 30.0

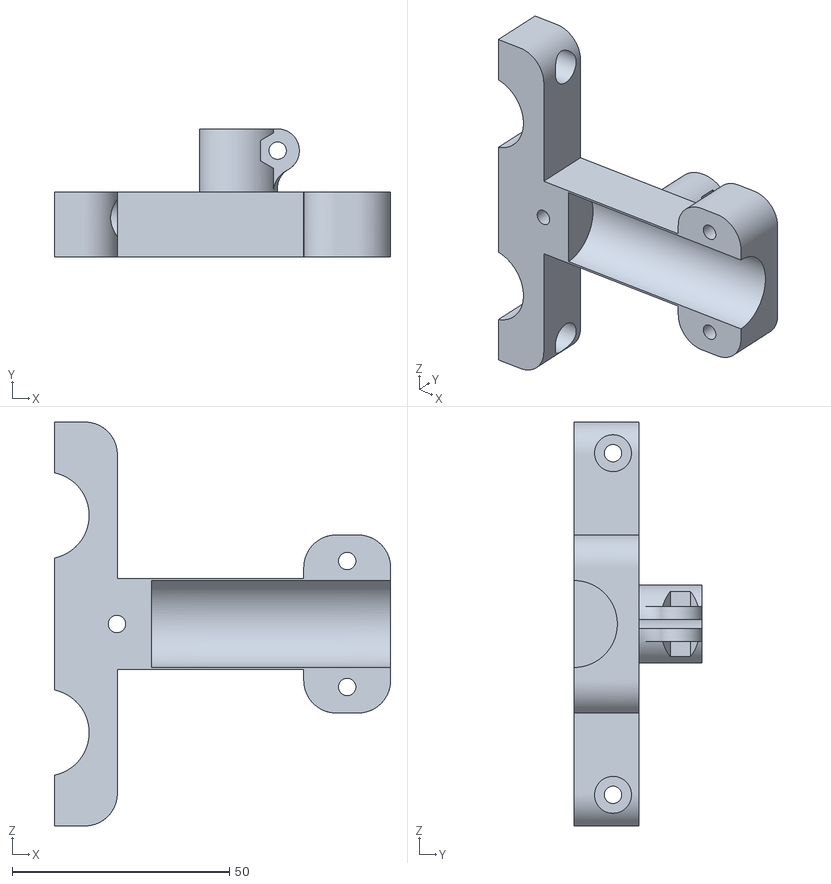
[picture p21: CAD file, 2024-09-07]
3 - Infinity/Files/EU - Metric 19mm pipe/gantry-idlers-rod-holder.stl
77.4 x 29.5 x 93.0

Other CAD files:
3 - Infinity/Files/Shared/bed-mounting-plate-48inchesbelt.dxf
3 - Infinity/Files/US - 12 US EMT conduit/frame-3xcorner-gantry-left.stl
4 - CoreXY Enclosed/EU/frame-4xcorner.stl
4 - CoreXY Enclosed/Shared/gantry-X-carriage.stl
1 - Bed Slinger/Files/EU - Metric 19mm pipe/2xcorner.19.9mm.stl
1 - Bed Slinger/Files/EU - Metric 19mm pipe/3xcorner L.stl
1 - Bed Slinger/Files/EU - Metric 19mm pipe/3xcorner R.stl
1 - Bed Slinger/Files/EU - Metric 19mm pipe/3xcorner_L.19.9mm.stl
1 - Bed Slinger/Files/EU - Metric 19mm pipe/3xcorner_R.19.9mm.stl
1 - Bed Slinger/Files/EU - Metric 19mm pipe/Extruder_Mount.19.9mm.stl
1 - Bed Slinger/Files/EU - Metric 19mm pipe/Tool_mount_sketch.dxf
1 - Bed Slinger/Files/EU - Metric 19mm pipe/X Motor Mount.stl
1 - Bed Slinger/Files/EU - Metric 19mm pipe/XRoller_alternative_UK.stl
1 - Bed Slinger/Files/EU - Metric 19mm pipe/X_Motor_Mount.19.9mm.stl
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

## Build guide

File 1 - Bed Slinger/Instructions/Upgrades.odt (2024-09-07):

# Upgrade to ACME screws

You may start upgrading you Piper 3d printer by installing ACME screws instead of 5/16 rods.

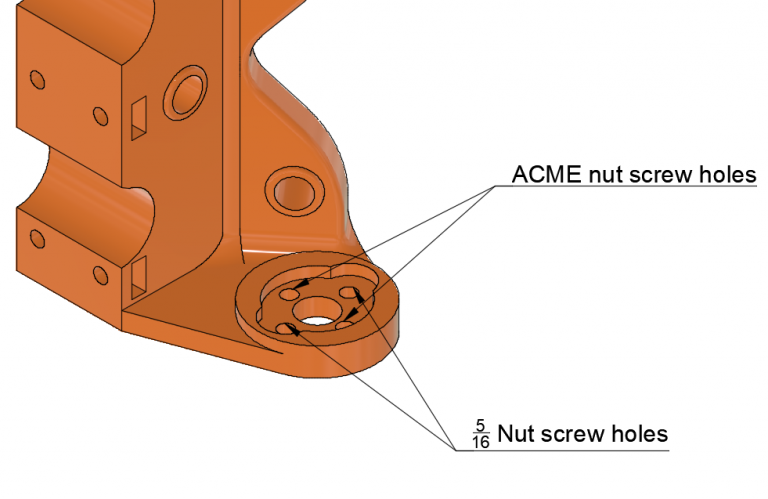
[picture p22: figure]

# Upgrade to heated bed.

To upgrade to heated bed you may have several options. Those options depend on the size of the bed.

Bed size | Heating element wattage | Heat bed voltage | Example of parts | Notes
200mm x 200mm | 200+ W | 12 V is sufficient | Heated bed (https://www.amazon.com/gp/product/B018XBWGHC/ref=oh_aui_detailpage_o00_s00?ie=UTF8&psc=1) | you need a separate SSR as Ramps 1.4 does not provide enough current
200mm x 300mm | 300+ W | You may need a separate PSU or move to 24V PSU | | may require changes to Ramps 1.4 board
300mm x 300mm | 450+ W | You need 110V(220V) heat panel, SSR DC to AC 25A and be very careful as moving pate will have wires with high voltage. | | This is not recommended configuration since wires with high voltage will be constantly bended by moving bed, failure in wires may cause electrical shock.

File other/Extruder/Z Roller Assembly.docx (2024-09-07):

Z Roller Assembly

Items needed for this step:

4 - Z_Roller.v1.1 (3D Bracket)

20 - 608 ball bearings (5 per Z Roller bracket)

16 - 5/16 1 inch or 25mm M8 bolts

4 - 5/16 1.5 inch or 40mm M8 bolts

20 - 5/16 or M8 nuts (Use thread locker or nylon nuts)

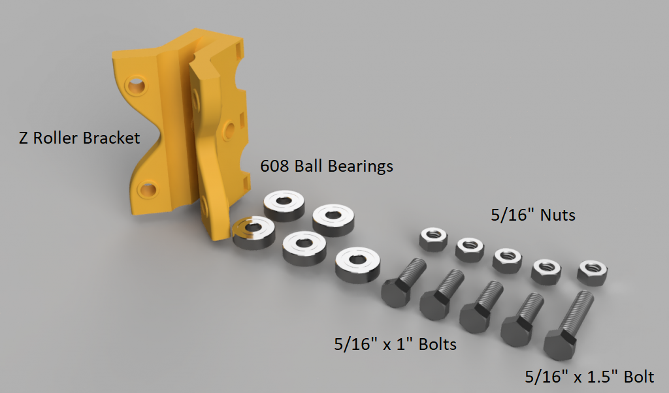
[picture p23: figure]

Separate the items as shown in the photo above: 1 - Z Roller, 5 – 608 ball bearings, 4 – 5/16” x 1” bolt, 1 – 5/16” x 1.5” bolt and 5 - 5/16” nuts.

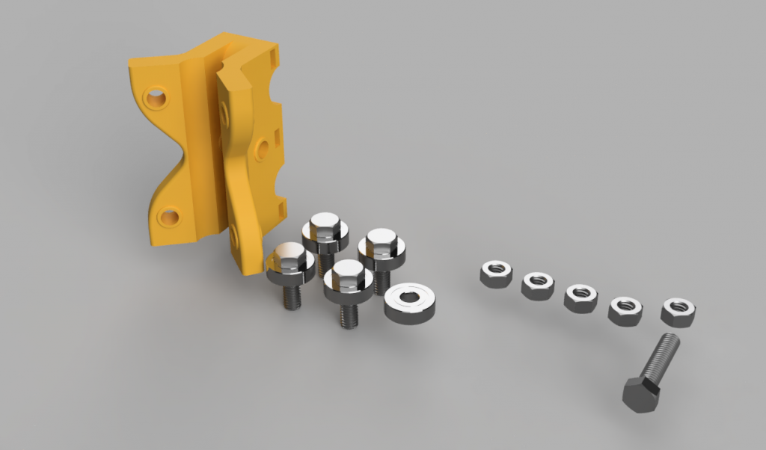
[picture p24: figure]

Place 1 – 608 ball bearing on each 5/16” x 1” bolt.

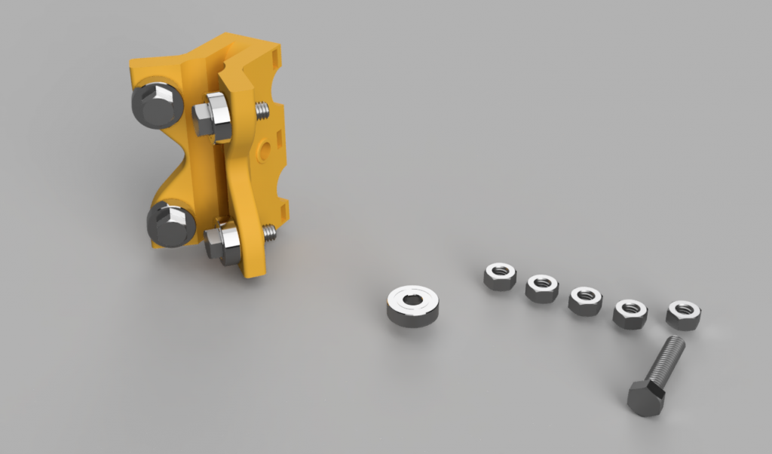
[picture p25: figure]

Install the 4 – 5/16”x1” bolt and 608 ball bearings in the Z Roller bracket as shown.

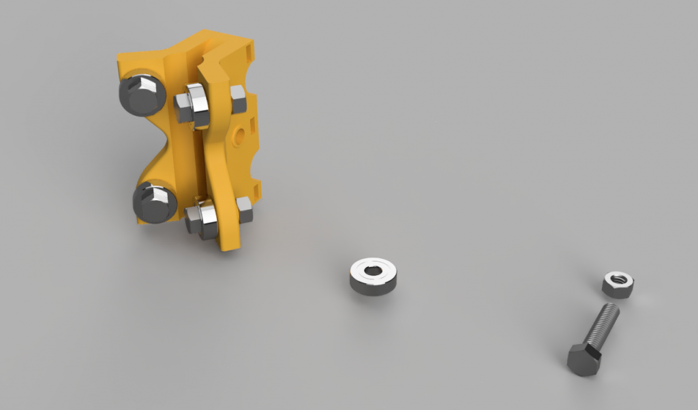
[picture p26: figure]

Screw 4 - 5/16” nuts on the 5/16” x1” bolt as shown. Use thread locker or nylon nuts.


Insert 1 – 608 ball bearing inside the Z Roller Bracket (middle channel) as shown.

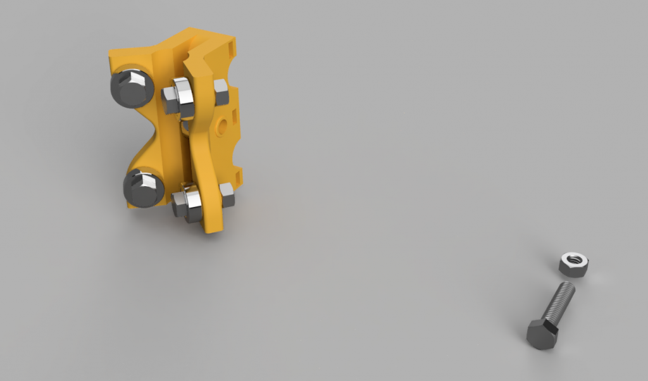
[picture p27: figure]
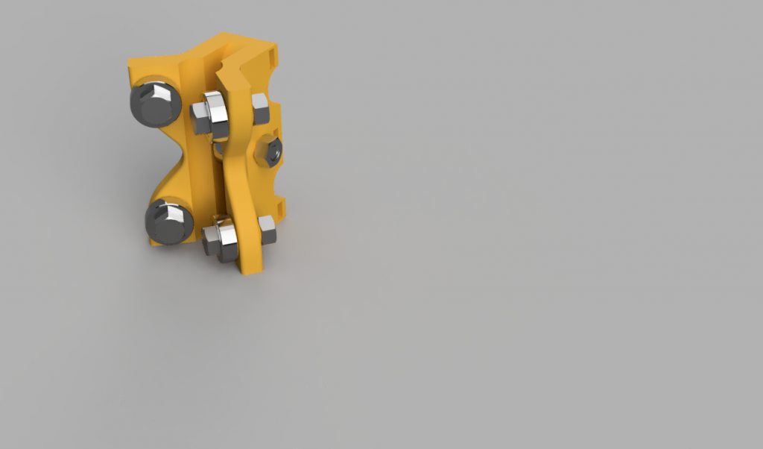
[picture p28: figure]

Insert the 5/16” x 1.5” bolt through the Z Roller bracket and through the 608 ball bearing. Once the bolt is inserted use the 5/16” nut on the 5/16” x 1.5 bolt as shown. Use thread locker or nylon nut.

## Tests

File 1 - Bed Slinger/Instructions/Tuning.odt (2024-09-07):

# Tuning

# Rollers.

A central bolt of the roller of Piper 1 is at the same time tuning mechanism. To increase tension with the pipe tighten the central bolt, to decrease let it free. Rollers Should be sliding on pipes with a small tension. All ballbearing should rotate during the move.

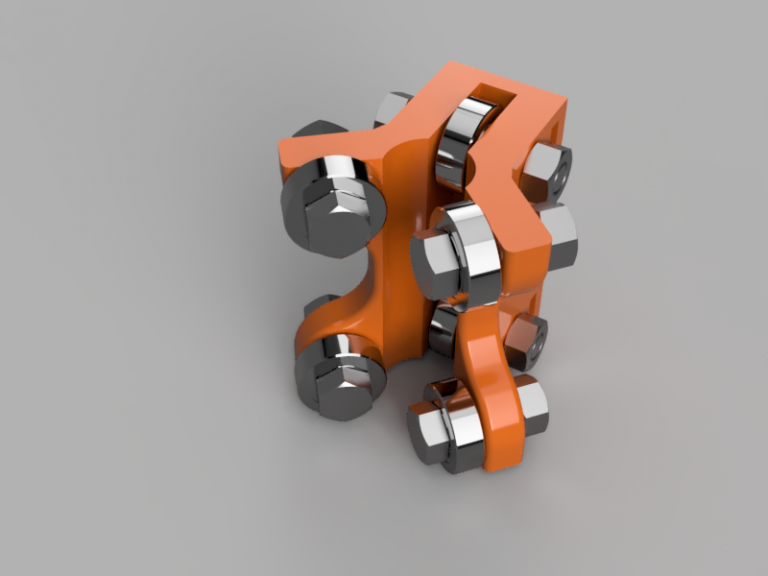
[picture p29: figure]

# Z axis.

After assembling the frame check that Z pipe is vertical. You may use any tool which allows measuring 90 degrees. Make necessary adjustments.

Make sure that Z rollers are tuned according to above instructions.
Untight top corner brackets on a pipe which is parallel to X-axis.
Move X gantry to the top position and temporary tie it to the top pipe (using rope or wire).
Tighten corner brackets.

# Z Rods

If you already connected rods to Z motors couplings remove them.
Move X gantry to the lowest position and check that Z rods (lead screw/ACME screw) are aligned with motor shafts. To adjust alignment you may move motor left right.

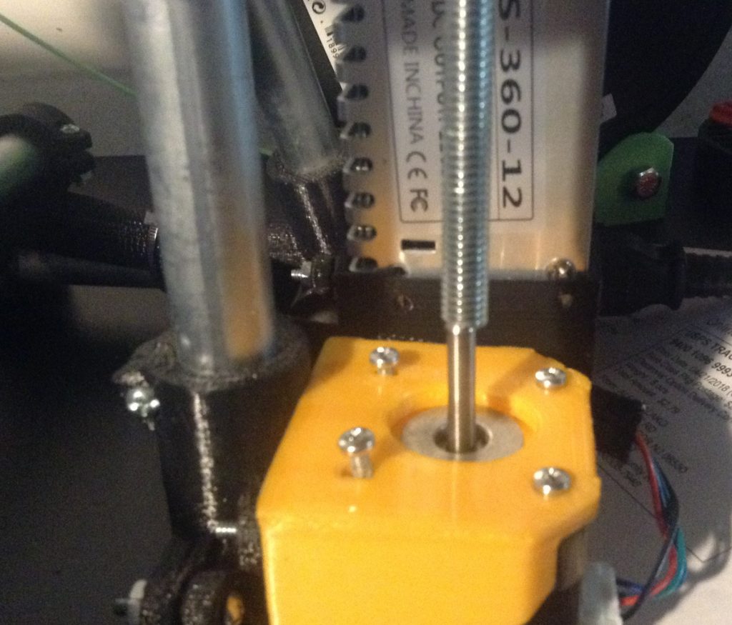
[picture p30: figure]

Once rods are aligned with motors you may attach pineapple coupling.

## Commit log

2024-09-07 attempt to cleanup and organize
    [10mm-belt-tensioner-500+.stl, 2x corner new v10.f3d, 2x corner new v16.f3d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]
2024-09-07 More organization
    [10mm-belt-tensioner-500+.stl, 6mm-belt-tensioner.stl, Corner.stl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]
